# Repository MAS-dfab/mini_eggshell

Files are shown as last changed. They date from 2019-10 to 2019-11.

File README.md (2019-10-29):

# mini_Eggshell

Repository for the MAS1920 T1 Miniproject: mini_Eggshell

## Groups:
1. Laszlo, Edurne, Eliott
2. Yuhung, Maria, Remy
3. Ping, Jomana, Indra
4. Anton, Fatemeh, Emmanuelle
5. Chanon, Ioulios, Fred
6. Mahiro, Dinorah

## Schedule

[Find the latest schedule on Google Spreadsheets](https://docs.google.com/spreadsheets/d/181aZo1s0SwAvfoG4fKHYC5BHTWoBZZNCnyvJNnxfnJw/edit?usp=sharing)

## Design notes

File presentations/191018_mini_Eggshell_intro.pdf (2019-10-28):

# mini_Eggshell

## MAS T1 | 28.10.2019

## Introduction

## Eggshell

## Previous Miniprojects

## Assignment

## Schedule

## Ur online control

# Content

Gramazio Kohler Research
ETH Zurich

# Introduction

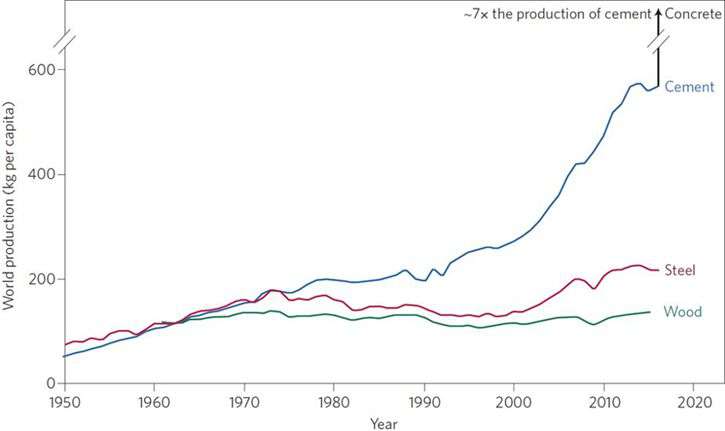
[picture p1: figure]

Gramazio Kohler Research

Paulo, Monteiro, Sabbie, Miller and Horvath (2017)

# Cost of a standard concrete element

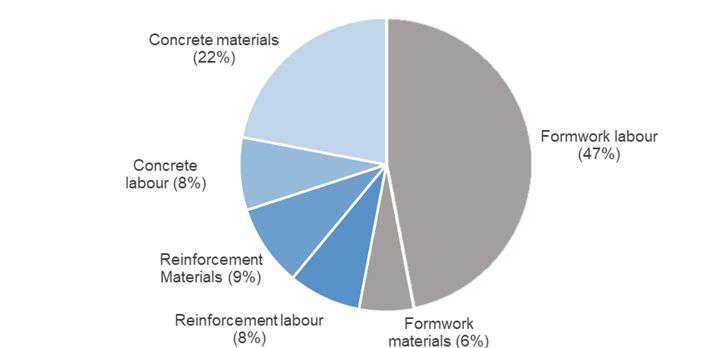
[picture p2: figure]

Gramazio Kohler Research

Lab (2007)

# Cost of a non-standard concrete element

Gramazio Kohler Research

Schipper and Grünewald (2014)

## xxx

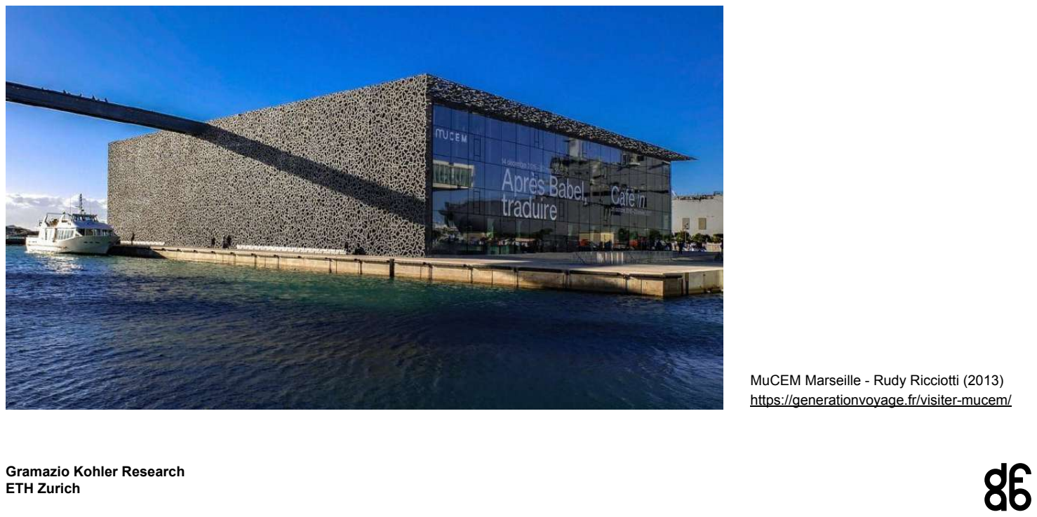
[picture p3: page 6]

Gramazio Kohler Research

MuCEM Marseille - Rudy Ricciotti (2013) https://generationvoyage.fr/visiter-mucem/

Gramazio Kohler Research

best of DETAIL 8 Beton/Concrete, Christian Schittich (2016)

# Eggshell concept

Gramazio Kohler Research

Ulrich (2017)

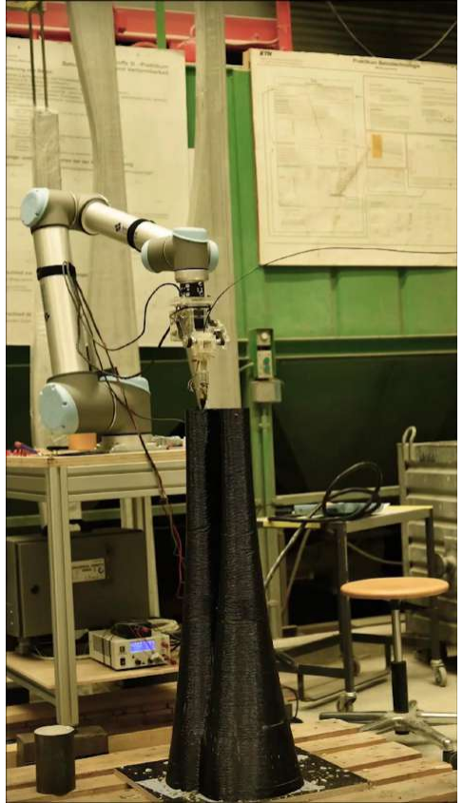
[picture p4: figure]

Gramazio Kohler Research

Gramazio Kohler Research (https://docs.google.com/file/d/1PcqgR71OjFk5ioSvPbPdr6lzZ_gwDWqv/preview)

# Simultaneous printing & filling

Gramazio Kohler Research

# Consecutive fabrication

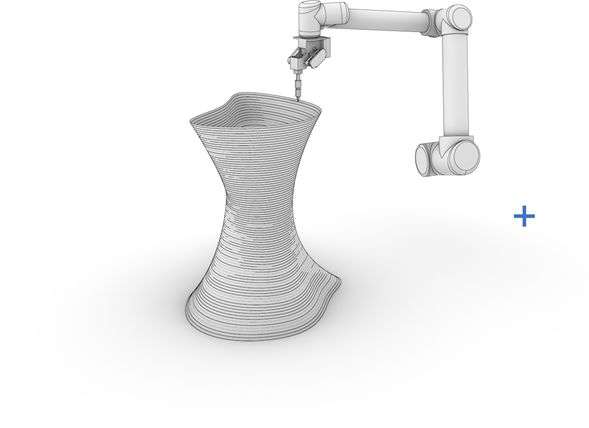
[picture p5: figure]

Gramazio Kohler Research

# Consecutive fabrication

Gramazio Kohler Research

# Consecutive fabrication

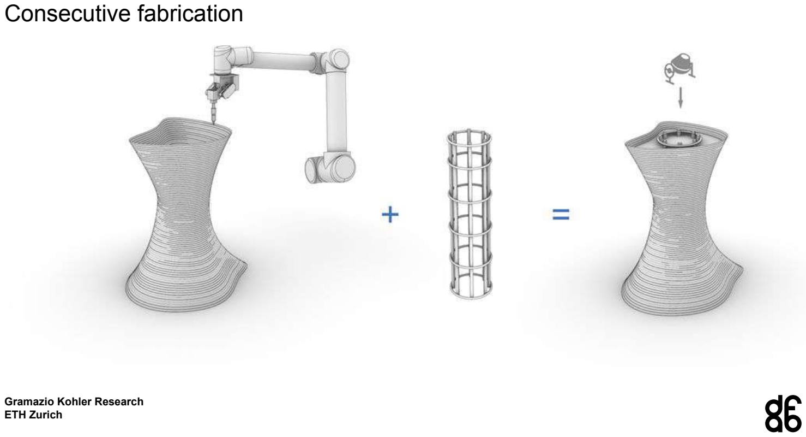
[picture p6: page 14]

Gramazio Kohler Research

# Basler & Hofmann

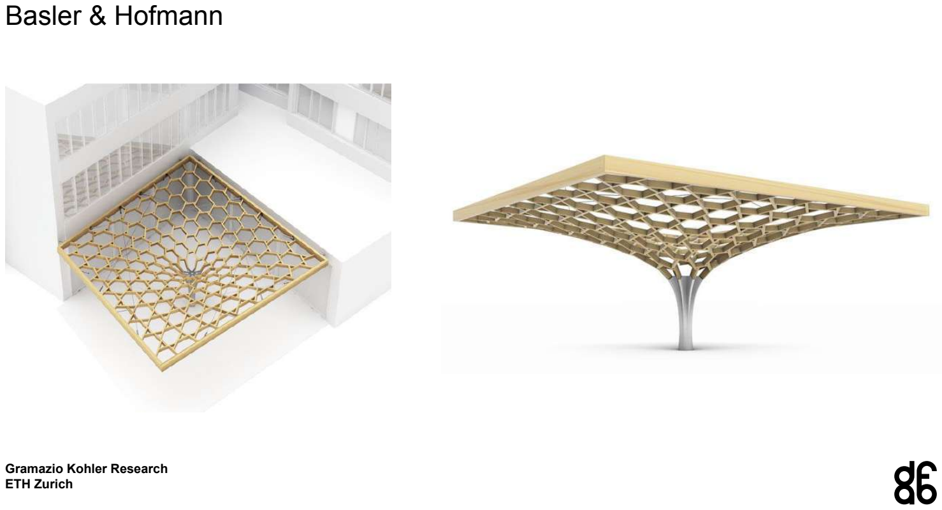
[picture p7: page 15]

Gramazio Kohler Research

Gramazio Kohler Research

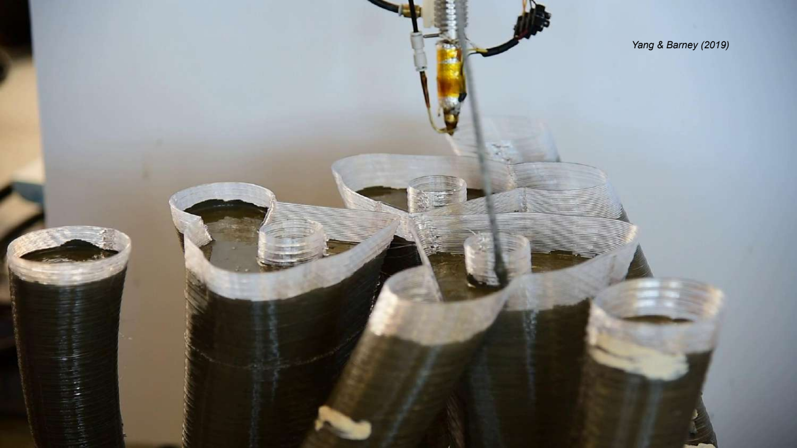
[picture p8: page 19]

Yang & Barney (2019) (https://docs.google.com/file/d/1zKKD6e-WPvSI6ZfkJOCtpLaU1aZg0VbD/preview)

minijammed is a three-week design and build assignment based on the ongoing research project Jammed Architectural Structures. The research focuses on the development of design and fabrication techniques to build fully reversible architectural structures by interlacing crushed-rock stones with textile string without any permanent bonding. The potential of the concept has been proven at architectural scale through the realisation of larger prototypes: Rock Print and Rock Print: A Manistone. minijammed invites the students to explore the design possibilities and the rich solution space of the method in a smaller scale.

The short-term project suggests a material-driven design and a robotic fabrication strategy, as only through the execution of multiple physical experiments, both manual and robotic, the designer is able to take informed decisions about the final outcome of the process.

# minijammed

Gramazio Kohler Research

Gramazio Kohler Research

minijammed: final exhibition

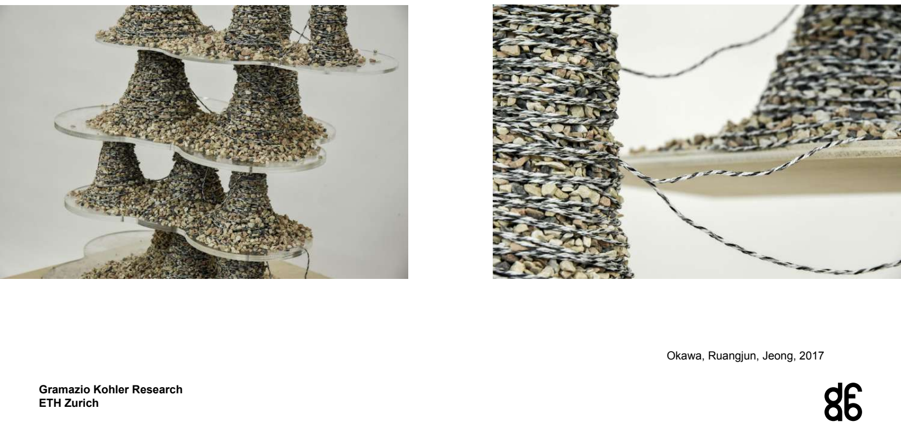
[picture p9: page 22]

Gramazio Kohler Research

Okawa, Ruangjun, Jeong, 2017

Gramazio Kohler Research

Pastrana, Su, Lin, Yoo, 2017

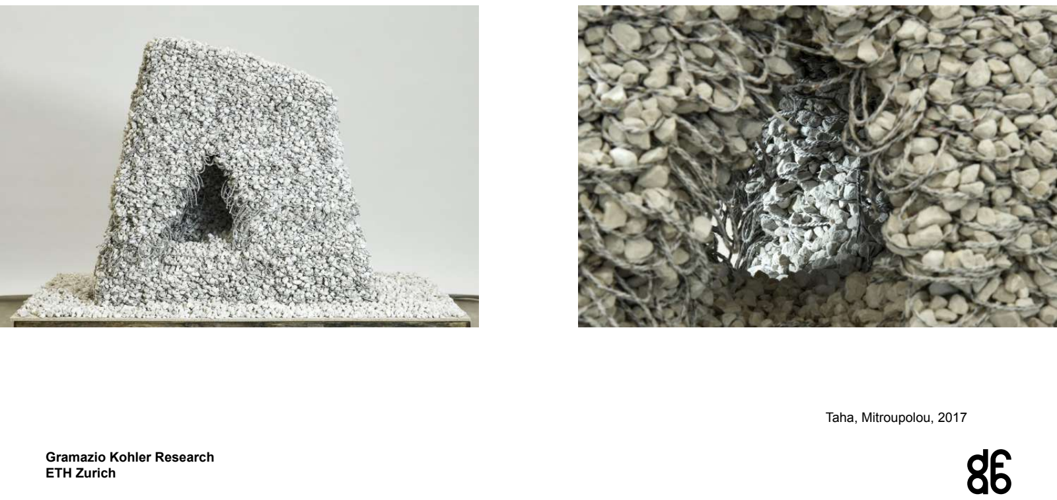
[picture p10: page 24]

Gramazio Kohler Research

Taha, Mitroupolou, 2017

Gramazio Kohler Research

Cena, Chousou, Wang, Wu, 2017

Rapid Clay Formations is a four-week design and build assignment investigating a novel fabrication process for malleable materials. Starting with the Remote Material Deposition installation in 2014, the Chair of Architecture and Digital Fabrication has investigated the idea of robotically positioning material in space from a distance and thereby creating differentiated architectural aggregations that are a direct expression of a dynamic and adaptive fabrication process. Continuing this concept, more recent projects developed within the MAS programme shifted the focus to the study of robotic fabrication processes for malleable materials, where the precise control of forces and positions applied to the material to design and build highly differentiated structures.

# Rapid Clay Formations

Gramazio Kohler Research

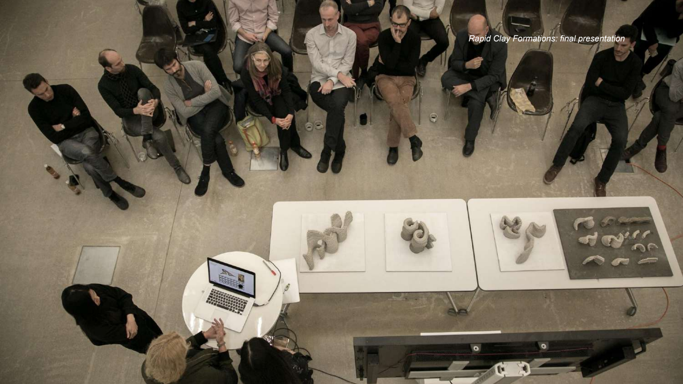
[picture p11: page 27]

Gramazio Kohler Research

Rapid Clay Formations: final presentation

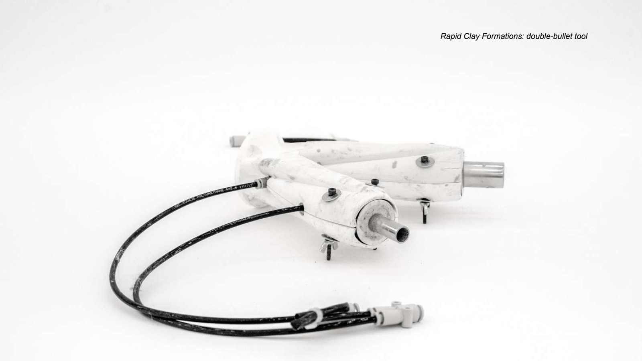
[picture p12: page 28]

Gramazio Kohler Research

Rapid Clay Formations: double-bullet tool

Gramazio Kohler Research

Akizuki, Barney, Du, 2018

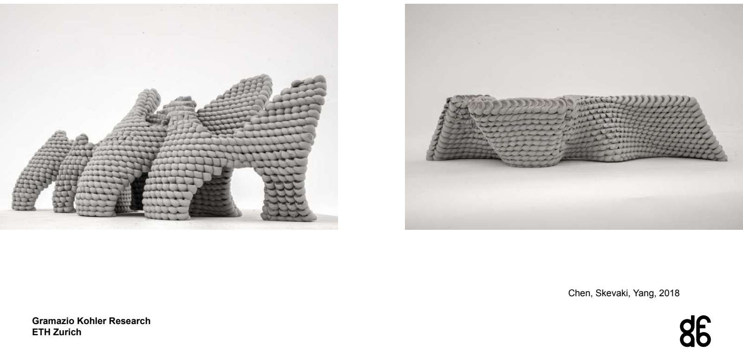
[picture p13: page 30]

Gramazio Kohler Research

Chen, Skevaki, Yang, 2018

Gramazio Kohler Research

v.d.Bulcke, Girish, Eftekhar, 2018

Use the Eggshell simultaneous printing & filling process to produce various building components.

## Two formwork material options

- | Clay | - 3 setups
- | Thermoplastic | - 3 setups

## Different building elements

## - Beam - Slab - Wall - Interface element (column - beam or wall - slab) - Column

# mini-eggshell: Assignment

Gramazio Kohler Research

## Focus on:

- | Structure | (reduce material/ weight, precise guides for reinforcement)
- | Function | (integrate different functions, lighting , media, electrical or mechanical services)
- | Performance | (integrate natural lighting and ventilation through transparency, porosity. Acoustics )
- | Aesthetics | (surface textures and ornamentation, architectural design, details)

# mini-eggshell: Goals

Gramazio Kohler Research

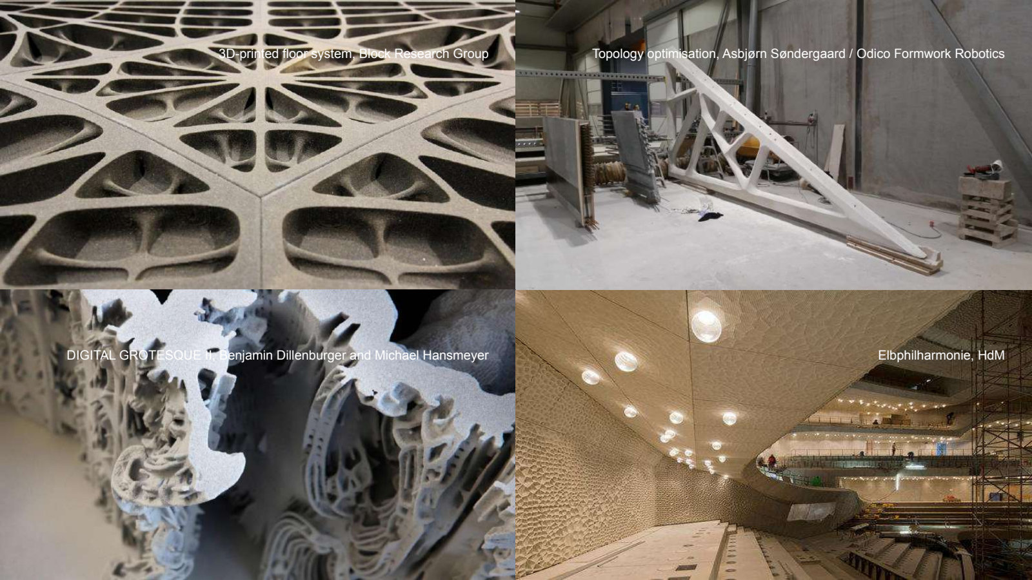
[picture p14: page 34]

3D-printed floor system, Block Research Group | Topology optimisation, Asbjørn Søndergaard / | Odico Formwork Robotics (https://www.odico.dk/?utm_medium=website&utm_source=archdaily.com)
DIGITAL GROTESQUE II, Benjamin Dillenburger and Michael Hansmeyer | Elbphilharmonie, HdM

# Schedule

Gramazio Kohler Research

https://docs.google.com/spreadsheets/d/181aZo1s0SwAvfoG4fKHYC5BHTWoBZZNCnyvJNnxfnJw/edit?usp=sharing

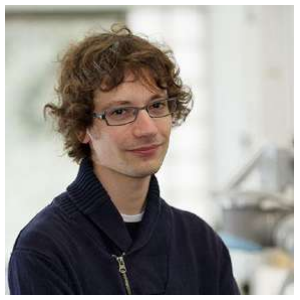
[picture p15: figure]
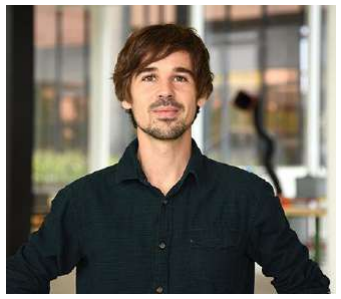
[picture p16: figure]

Dr. Lex Reiter (post-doc in PCBM) | Lukas Gebhard (PhD student with IBK) | Dr. Thibault Demoulin (post-doc at PCBM and Oxara)

# Guest Lectures

Gramazio Kohler Research

## - Grasshopper

# UR Online Control

### - JSON (https://en.wikipedia.org/wiki/JSON)

## - Python main file

Gramazio Kohler Research

# UR Online Control

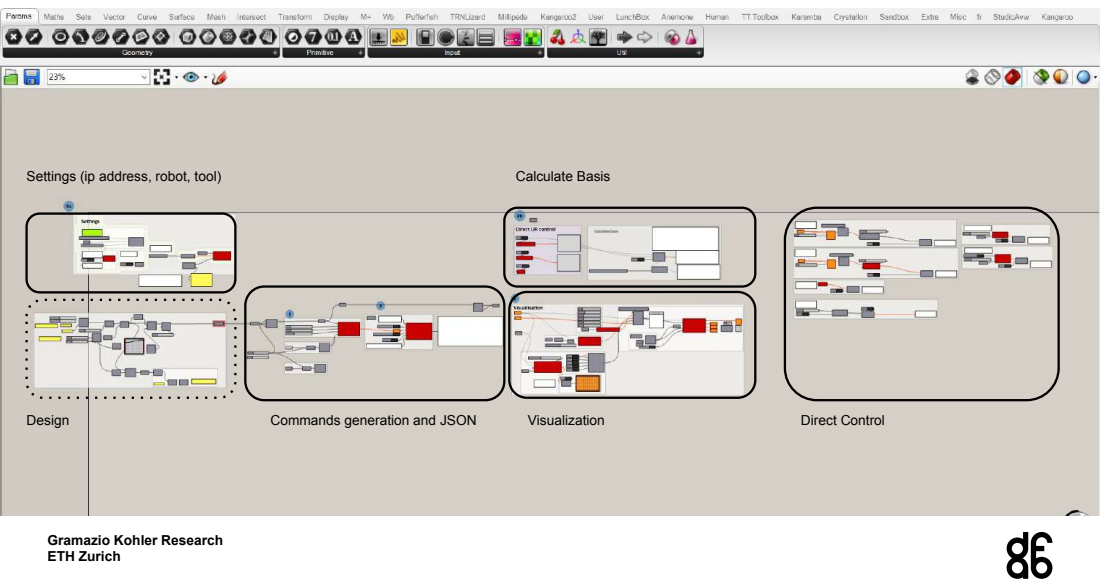
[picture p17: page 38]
Design; Commands generation and JSON; Visualization; Direct Control; Calculate Basis

Settings (ip address, robot, tool)

Gramazio Kohler Research

# UR Online Control

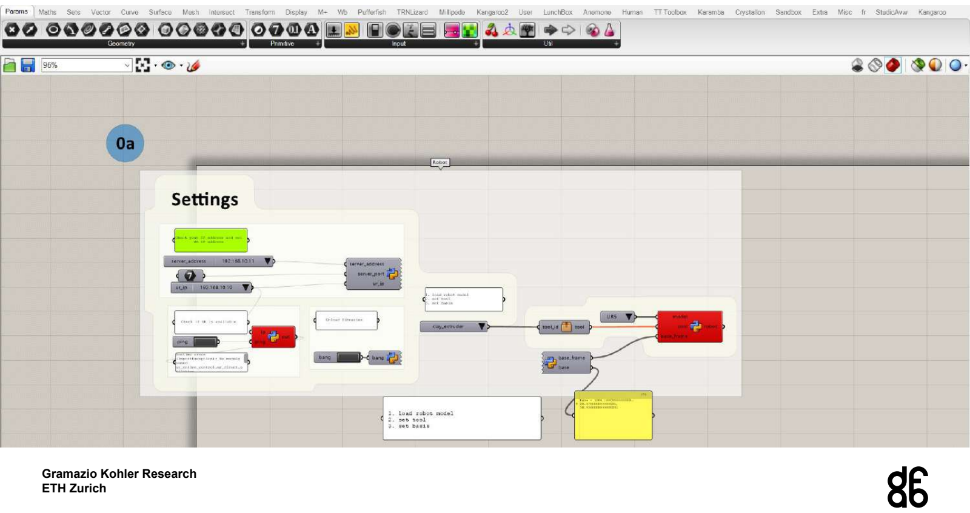
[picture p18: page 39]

Gramazio Kohler Research

# UR Online Control

Gramazio Kohler Research

# UR Online Control

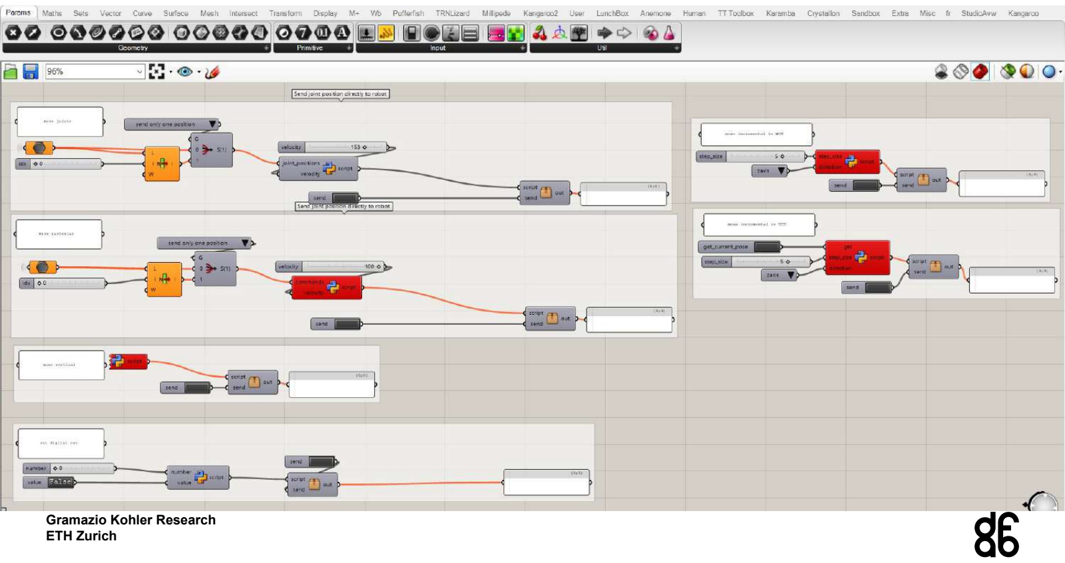
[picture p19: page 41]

Gramazio Kohler Research

# UR Online Control

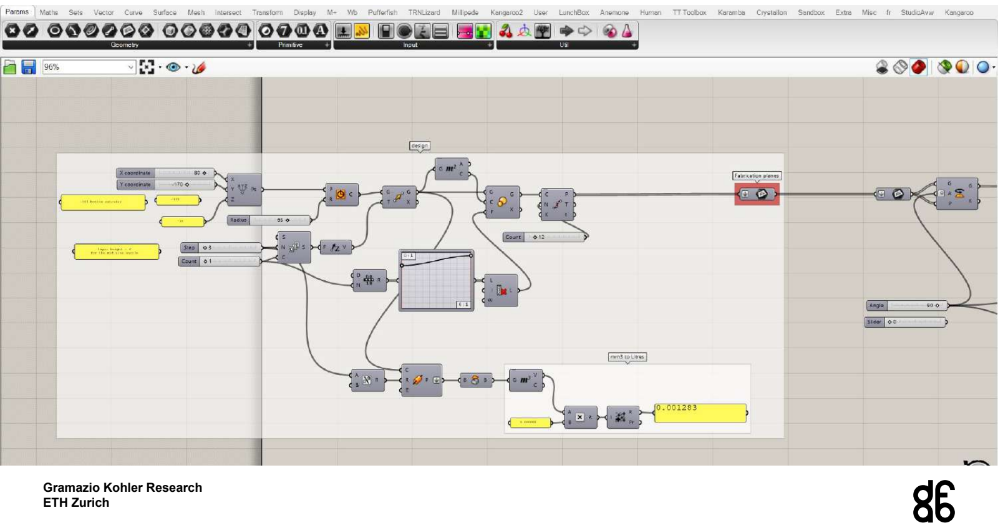
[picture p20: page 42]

Gramazio Kohler Research

# UR Online Control

Gramazio Kohler Research

# UR Online Control

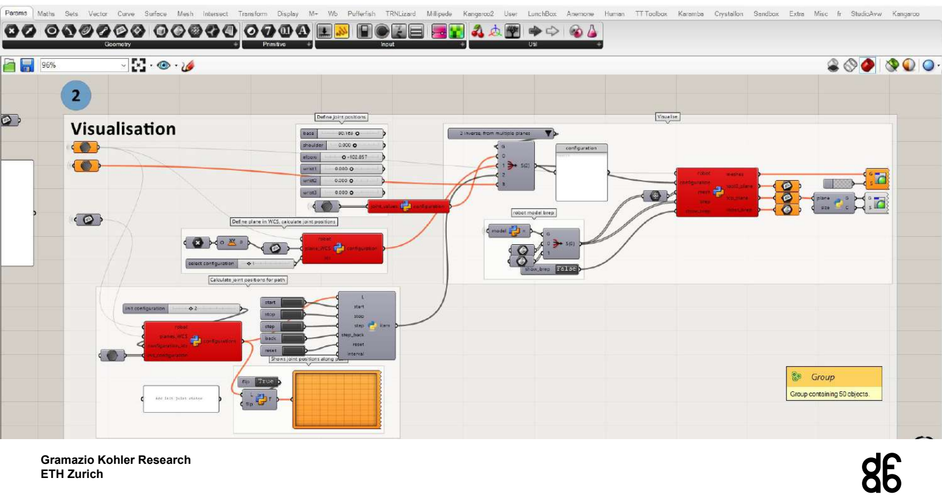
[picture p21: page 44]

Gramazio Kohler Research

# UR Online Control

Gramazio Kohler Research

# UR Online Control

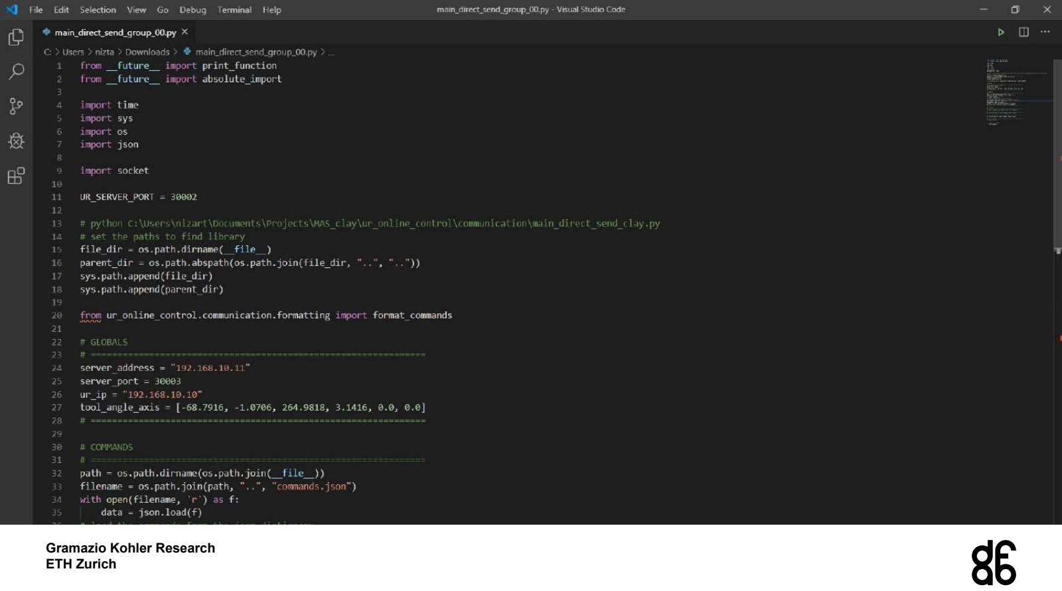
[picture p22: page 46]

Gramazio Kohler Research

# UR Online Control

Gramazio Kohler Research

# UR Online Control

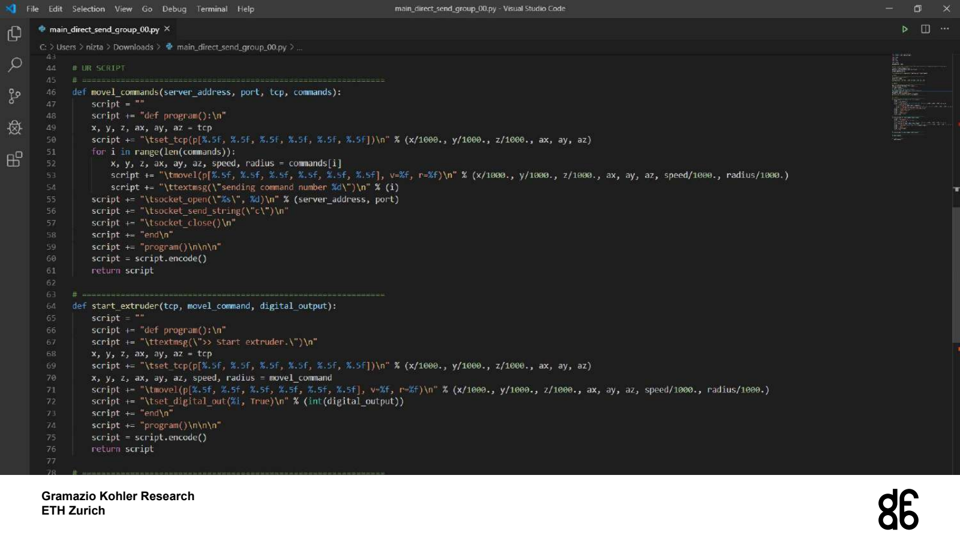
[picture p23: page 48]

Gramazio Kohler Research

# UR Online Control

Gramazio Kohler Research

# UR Online Control

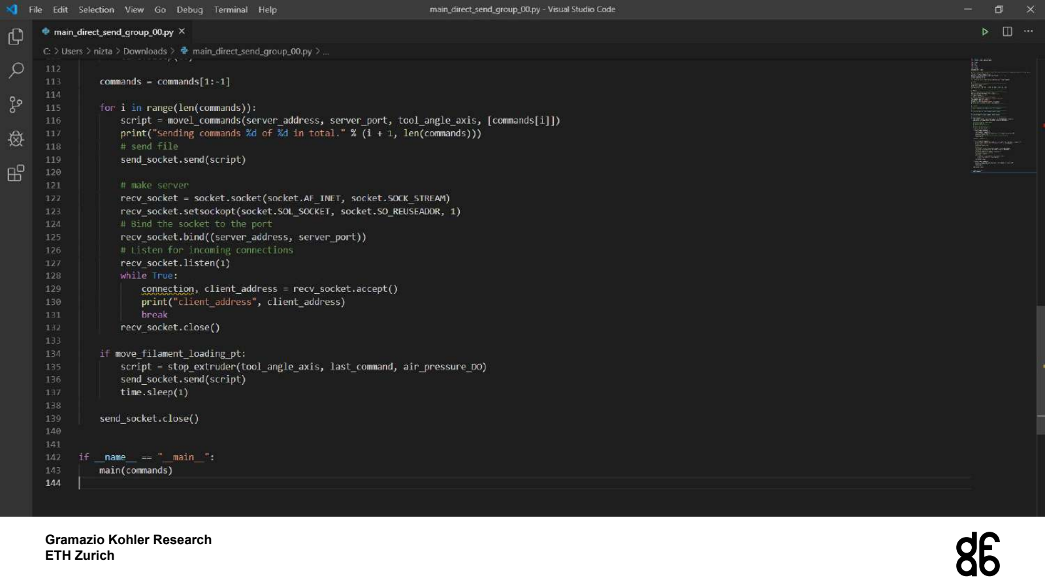
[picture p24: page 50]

Gramazio Kohler Research

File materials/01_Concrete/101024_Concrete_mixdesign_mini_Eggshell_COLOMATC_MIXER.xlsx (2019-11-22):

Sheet: M6
Mixture:
 |  | Weight | Density | Water content | Volume parts | Water weight |  | 1L
Sand | 0-4mm | 740 | 2.63 | 0 | 281.37 | 0 |  | 636.63
Cement | Normo5R | 982 | 3.1 | 0 | 316.77 | 0 |  | 844.83
Fly ash | Hydrolent | 165 | 2.3 | 0 | 71.74 | 0 |  | 141.95
Silicafume | MS 971U | 93 | 2.2 | 0 | 42.27 | 0 |  | 80.01
PVA 6mm | 6/0.15 | 13 | 1.3 | 0 | 10.00 | 0 |  | 11.18
PVA 12mm | 12/0.2 | 13 | 1.3 | 0 | 10.00 | 0 |  | 11.18
Water | Tap | 371 | 1 | 100 | 371.00 | 371 |  | 319.18
Superplasticizer | Glenium ACE30 | 4 | 1.06 | 70 | 3.77 | 2.8 |  | 3.44
Retarder | Succrose 30% | 2.7 | 1.05 | 70 | 2.57 | 1.89 |  | 2.32
Accelerator | X-Seed 100 | 60 | 1.135 | 78.5 | 52.86 | 47.1 |  | 51.62
 | SUM | 2443.7 | 2.102354706 |  | SUM | 422.79
 | V | 1162.363322
 | Exact calculation
 | Composition |  |  |  |  |  | Cement paste |  |  |  | Calculated properties: |  |  |  | Component properties: |  |  |  |  |  |  |  | 1 volume is mass of | On the volume given |  | mass
V | 30000 | mL |  |  |  |  | V [mL] | 14400 |  |  | Density [kg/m3] | 1912.0 |  |  |  | Density: | Solid content |  | Weight pure parts | Weight solution | Weight water | Volume solution | Solution | Solution | Solid | Water
Sand | 52 | % | Volume parts, all |  |  |  | w/b [-] | 0.4 | b |  | w/c [-] | 0.400 |  |  | CEM | 3.1 | 1 |  | 1 | 1 | 0 | 0.3225806452 | 1.234029847 | 17770.03 | 17770.03 | 0.00
PVA 6mm | 0 | % | Volume parts, all |  |  |  | FA[%] | 0 | b |  | Total weight [g]: | 27533.12 |  |  | FA | 2.3 | 1 |  | 0 | 0 | 0 | 0 | 0 | 0.00 | 0.00 | 0.00
PVA 12mm | 0 | % | Volume parts, all |  |  |  | MS[%] | 8 | b |  | Binder [g]: | 19315.25 |  |  | MS | 2.2 | 1 |  | 0.08695652174 | 0.08695652174 | 0 | 0.0395256917 | 0.1073069433 | 1545.22 | 1545.22 | 0.00
CEM | 92 | % | Weight binder |  |  |  | SP Glenium | 0.87 | b |  | All water [g] | 7726.10 |  |  | H20 | 1 | 0 | total | 0.4347826087 | 0.4057173913 | 0.4057173913 | 0.4057173913 | 0.5006673705 | 7209.61 | 0.00 | 7209.61
FA | 0 | % | Weight binder |  |  |  | RT | 0.35 | b |  |  |  |  |  | GleniumACE | 1.06 | 0.3 |  | 0.002836956522 | 0.009456521739 | 0.006619565217 | 0.008921246924 | 0.01166963008 | 168.04 | 50.41 | 117.63
MS | 8 | % | Weight binder |  |  |  | X-Seed | 0 | b |  |  |  |  |  | RT | 1.05 | 0.3 |  | 0.001141304348 | 0.003804347826 | 0.002663043478 | 0.003623188406 | 0.004694678768 | 67.60 | 20.28 | 47.32
Water | 0.4 | - | wb |  |  |  | C-100 | 4 | b |  |  |  |  |  | AC | 1.135 | 0.215 |  | 0 | 0 | 0 | 0 | 0 | 0.00 | 0.00 | 0.00
SP | 0.87 | % | weight_solution_adm/weight_dry_binder |  |  |  | Recipe: | weight [g]: |  | Content [kg/m3cementpaste] |  |  |  |  | C-100 | 1.45 | 0.545 |  | 0.02369565217 | 0.04347826087 | 0.0197826087 | 0.0299850075 | 0.05365347163 | 772.61 | 421.07 | 351.54
RT | 0.35 | % | weight_solution_adm/weight_dry_binder |  |  |  | CEM | 17770.03 |  | 1234.03 | as solution
X-Seed 100 | 0 | % | weight_solution_adm/weight_dry_binder |  |  |  | FA | 0.00 |  | 0.00 |  |  |  |  |  |  |  | SUM | 1.549413043 |  | 0.4347826087 | 0.810353171 |  |  |  | 7726.10
C-100 | 4 | % | weight_solution_adm/weight_dry_binder |  |  |  | MS | 1545.22 |  | 107.31
 | Components |  |  |  |  |  | H2O | 7209.61 |  | 500.67 |  |  |  |  |  |  |  |  | Weight binder
Sand | 0-4mm | 2.63 | 0 |  |  |  | ACE30 | 168.04 |  | 11.67 |  |  |  |  |  |  |  |  | 1.086956522
CEM | Normo5R | 3.1 | 0 |  |  |  | RT | 67.60 |  | 4.69
FA | Hydrolent | 2.3 | 0 |  |  |  | AC | 0.00 |  | 0.00
MS | MS 971U | 2.2 | 0 |  |  |  | C-100 | 772.61 |  | 53.65 |  |  |  |  | Mortar component volumes
H2O | Tap | 1 | 100 |  |  |  | Mortar |  |  |  |  |  |  |  | Volume | Weight | Density
ACE30 | Glenium ACE30 | 1.06 | 70 |  |  |  | V [mL] | 30000 |  |  |  |  |  |  | 14400 | 27533.12 | 1.91
RT | Succrose 30% | 1.05 | 70 |  |  |  | C_Sand | 52 | % |  |  |  |  |  | 15600 | 41028 | 2.63
AC | X-Seed 100 | 1.135 | 78.5 |  |  |  | C_PVA6mm | 0 | % |  |  |  |  |  | 0 | 0 | 1.30
C-100 | C-100 | 1.45 | 45.5 |  |  |  | C_PVA12mm | 0 | % |  |  |  |  |  | 0 | 0 | 1.30
PVA6mm | 6/0.15 | 1.3 | 0 |  |  |  |  |  |  | solution | pure
PVA12mm | 12/0.2 | 1.3 | 0 |  |  |  | Recipe | g | (6L) | Content [kg/m3mortar] | Content | Volume | Before acceleration
 |  |  |  |  |  |  | Sand | 41028.00 |  | 1367.60 | 1367.60 | 520.00 | wb | 0.377
 |  |  |  |  |  |  | CEM | 17770.03 |  | 592.33 | 592.33 | 191.08
 | 0.0649 |  |  |  |  |  | FA | 0.00 |  | 0.00 | 0.00 | 0.00
 | 1.0403 | 0.3467666667 |  |  |  |  | MS | 1545.22 |  | 51.51 | 51.51 | 23.41
 | 2.027 | 1.351333333 |  |  |  |  | H2O | 7209.61 |  | 240.32 | 257.54 | 240.32
 |  |  |  |  |  |  | ACE30 | 168.04 |  | 5.60 | 1.68 | 5.28
 |  |  |  |  |  |  | Sucrose | 67.60 |  | 2.25 | 0.68 | 2.15
 |  |  |  |  |  |  | X-Seed | 0.00 |  | 0.00 | 0.00 | 0.00
 |  |  |  |  |  |  | C-100 | 772.61 |  | 25.75 | 14.04 | 17.76
Used compositions:
Standard Mixture:
V | 1000
Sand | 24.21
PVA 6mm | 0.8603
PVA 12mm | 0.8603
CEM | 79.19
FA | 13.31 |  |  |  |  |  |  |  | Density | 2285.37 | kg/m3
MS | 7.5
Water | 0.341
SP | 0.0968
RT | 0.0653
AC | 1.0403
Print this:
 | Composition
V | 30000 | mL
Sand | 52 | % | Volume parts, all
PVA 6mm | 0 | % | Volume parts, all
PVA 12mm | 0 | % | Volume parts, all
CEM | 92 | % | Weight binder
FA | 0 | % | Weight binder
MS | 8 | % | Weight binder
Water | 0.4 | - | wb
SP | 0.87 | % | weight_solution_adm/weight_dry_binder
RT | 0.35 | % | weight_solution_adm/weight_dry_binder
X-Seed 100 | 0 | % | weight_solution_adm/weight_dry_binder
C-100 | 4 | % | weight_solution_adm/weight_dry_binder
Recipe | Mass [g] | 30 | L
Sand | 41028.0
CEM | 17770.0
FA | 0.0
MS | 1545.2
H2O | 7209.6
ACE30 | 168.04
Sucrose | 67.60
X-Seed | 0.00
C-100 | 772.61

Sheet: Print
 |  | Composition
Volume |  | 30000 | mL | <--- edit this field |  | MIXDESIGN FOR COLOMATIC MIXER (LESS SP)
AGGREGATES
Sand | 0-4mm | 52 | %
Cement | Normo 5R | 92 | % |  |  | ACCELERATION TABLE
Microsilica | Masterlife | 8 | % |  |  | For these liters of final product | 0.10 | L | For these liters of final product | 1.00 | L
 |  |  |  |  |  | Mass of retarded | 0.229 | kg | Mass of retarded | 2.285 | kg
ADMIXTURES |  |  |  |  |  | Mass of accelerator C-100 | 2.45 | g | Mass of accelerator C-100 | 24.53 | g
Water |  | 0.4 | -
Superplasticizer | BASF MasterGlenium ACE30 | 0.87 | % |  |  | For these liters of final product | 0.25 | L | For these liters of final product | 2.00 | L
Sucrose | 70% water / 30% sugar | 0.35 | % |  |  | Mass of retarded | 0.571 | kg | Mass of retarded | 4.571 | kg
 |  |  |  |  |  | Mass of accelerator C-100 | 6.13 | g | Mass of accelerator C-100 | 49.06 | g
ACCELERATOR
Accelerator | SIKA C-100 | 4 | % |  |  | For these liters of final product | 0.50 | L | For these liters of final product | 3.00 | L
 |  |  |  |  |  | Mass of retarded | 1.143 | kg | Mass of retarded | 6.856 | kg
Recipe |  | Mass [g] |  |  |  | Mass of accelerator C-100 | 12.27 | g | Mass of accelerator C-100 | 73.59 | g
AGGREGATES
Sand | 0-4mm | 41028.0 | g
Cement | Normo 5R | 17770.0 | g
Microsilica | Masterlife | 1545.2 | g
ADMIXTURES
Water |  | 7209.6 | g
Superplasticizer | BASF MasterGlenium ACE30 | 168.04 | g
Sucrose | 70% water / 30% sugar | 67.60 | g
ACCELERATOR
Accelerator | SIKA C-100 | 772.61 | g
Sum of mass |  | 68561.1 | Density | 2.29 | g/cm3
Accelerator amount |  |  | 24.53 | g/L
Mass before acceleration |  |  | 67788.5 | g
Mass of accelerator |  |  | 772.61 | g

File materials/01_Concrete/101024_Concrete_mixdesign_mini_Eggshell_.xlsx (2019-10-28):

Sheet: M6
Mixture:
 |  | Weight | Density | Water content | Volume parts | Water weight |  | 1L
Sand | 0-4mm | 740 | 2.63 | 0 | 281.37 | 0 |  | 636.63
Cement | Normo5R | 982 | 3.1 | 0 | 316.77 | 0 |  | 844.83
Fly ash | Hydrolent | 165 | 2.3 | 0 | 71.74 | 0 |  | 141.95
Silicafume | MS 971U | 93 | 2.2 | 0 | 42.27 | 0 |  | 80.01
PVA 6mm | 6/0.15 | 13 | 1.3 | 0 | 10.00 | 0 |  | 11.18
PVA 12mm | 12/0.2 | 13 | 1.3 | 0 | 10.00 | 0 |  | 11.18
Water | Tap | 371 | 1 | 100 | 371.00 | 371 |  | 319.18
Superplasticizer | Glenium ACE30 | 4 | 1.06 | 70 | 3.77 | 2.8 |  | 3.44
Retarder | Succrose 30% | 2.7 | 1.05 | 70 | 2.57 | 1.89 |  | 2.32
Accelerator | X-Seed 100 | 60 | 1.135 | 78.5 | 52.86 | 47.1 |  | 51.62
 | SUM | 2443.7 | 2.102354706 |  | SUM | 422.79
 | V | 1162.363322
 | Exact calculation
 | Composition |  |  |  |  |  | Cement paste |  |  |  | Calculated properties: |  |  |  | Component properties: |  |  |  |  |  |  |  | 1 volume is mass of | On the volume given |  | mass
V | 10000 | mL |  |  |  |  | V [mL] | 4800 |  |  | Density [kg/m3] | 1912.0 |  |  |  | Density: | Solid content |  | Weight pure parts | Weight solution | Weight water | Volume solution | Solution | Solution | Solid | Water
Sand | 52 | % | Volume parts, all |  |  |  | w/b [-] | 0.4 | b |  | w/c [-] | 0.400 |  |  | CEM | 3.1 | 1 |  | 1 | 1 | 0 | 0.3225806452 | 1.233969418 | 5923.05 | 5923.05 | 0.00
PVA 6mm | 0 | % | Volume parts, all |  |  |  | FA[%] | 0 | b |  | Total weight [g]: | 9177.55 |  |  | FA | 2.3 | 1 |  | 0 | 0 | 0 | 0 | 0 | 0.00 | 0.00 | 0.00
PVA 12mm | 0 | % | Volume parts, all |  |  |  | MS[%] | 8 | b |  | Binder [g]: | 6438.10 |  |  | MS | 2.2 | 1 |  | 0.08695652174 | 0.08695652174 | 0 | 0.0395256917 | 0.1073016885 | 515.05 | 515.05 | 0.00
CEM | 92 | % | Weight binder |  |  |  | SP Glenium | 0.885 | b |  | All water [g] | 2575.24 |  |  | H20 | 1 | 0 | total | 0.4347826087 | 0.4056032609 | 0.4056032609 | 0.4056032609 | 0.5005020198 | 2402.41 | 0.00 | 2402.41
FA | 0 | % | Weight binder |  |  |  | RT | 0.35 | b |  |  |  |  |  | GleniumACE | 1.06 | 0.3 |  | 0.002885869565 | 0.009619565217 | 0.006733695652 | 0.009075061526 | 0.01187024929 | 56.98 | 17.09 | 39.88
MS | 8 | % | Weight binder |  |  |  | X-Seed | 0 | b |  |  |  |  |  | RT | 1.05 | 0.3 |  | 0.001141304348 | 0.003804347826 | 0.002663043478 | 0.003623188406 | 0.004694448874 | 22.53 | 6.76 | 15.77
Water | 0.4 | - | wb |  |  |  | C-100 | 4 | b |  |  |  |  |  | AC | 1.135 | 0.215 |  | 0 | 0 | 0 | 0 | 0 | 0.00 | 0.00 | 0.00
SP | 0.885 | % | weight_solution_adm/weight_dry_binder |  |  |  | Recipe: | weight [g]: |  | Content [kg/m3cementpaste] |  |  |  |  | C-100 | 1.45 | 0.545 |  | 0.02369565217 | 0.04347826087 | 0.0197826087 | 0.0299850075 | 0.05365084427 | 257.52 | 140.35 | 117.17
RT | 0.35 | % | weight_solution_adm/weight_dry_binder |  |  |  | CEM | 5923.05 |  | 1233.97 | as solution
X-Seed 100 | 0 | % | weight_solution_adm/weight_dry_binder |  |  |  | FA | 0.00 |  | 0.00 |  |  |  |  |  |  |  | SUM | 1.549461957 |  | 0.4347826087 | 0.8103928552 |  |  |  | 2575.24
C-100 | 4 | % | weight_solution_adm/weight_dry_binder |  |  |  | MS | 515.05 |  | 107.30
 | Components |  |  |  |  |  | H2O | 2402.41 |  | 500.50 |  |  |  |  |  |  |  |  | Weight binder
Sand | 0-4mm | 2.63 | 0 |  |  |  | ACE30 | 56.98 |  | 11.87 |  |  |  |  |  |  |  |  | 1.086956522
CEM | Normo5R | 3.1 | 0 |  |  |  | RT | 22.53 |  | 4.69
FA | Hydrolent | 2.3 | 0 |  |  |  | AC | 0.00 |  | 0.00
MS | MS 971U | 2.2 | 0 |  |  |  | C-100 | 257.52 |  | 53.65 |  |  |  |  | Mortar component volumes
H2O | Tap | 1 | 100 |  |  |  | Mortar |  |  |  |  |  |  |  | Volume | Weight | Density
ACE30 | Glenium ACE30 | 1.06 | 70 |  |  |  | V [mL] | 10000 |  |  |  |  |  |  | 4800 | 9177.55 | 1.91
RT | Succrose 30% | 1.05 | 70 |  |  |  | C_Sand | 52 | % |  |  |  |  |  | 5200 | 13676 | 2.63
AC | X-Seed 100 | 1.135 | 78.5 |  |  |  | C_PVA6mm | 0 | % |  |  |  |  |  | 0 | 0 | 1.30
C-100 | C-100 | 1.45 | 45.5 |  |  |  | C_PVA12mm | 0 | % |  |  |  |  |  | 0 | 0 | 1.30
PVA6mm | 6/0.15 | 1.3 | 0 |  |  |  |  |  |  | solution | pure
PVA12mm | 12/0.2 | 1.3 | 0 |  |  |  | Recipe | g | (6L) | Content [kg/m3mortar] | Content | Volume | Before acceleration
 |  |  |  |  |  |  | Sand | 13676.00 |  | 1367.60 | 1367.60 | 520.00 | wb | 0.377
 |  |  |  |  |  |  | CEM | 5923.05 |  | 592.31 | 592.31 | 191.07
 | 0.0649 |  |  |  |  |  | FA | 0.00 |  | 0.00 | 0.00 | 0.00
 | 1.0403 | 0.3467666667 |  |  |  |  | MS | 515.05 |  | 51.50 | 51.50 | 23.41
 | 2.027 | 1.351333333 |  |  |  |  | H2O | 2402.41 |  | 240.24 | 257.52 | 240.24
 |  |  |  |  |  |  | ACE30 | 56.98 |  | 5.70 | 1.71 | 5.38
 |  |  |  |  |  |  | Sucrose | 22.53 |  | 2.25 | 0.68 | 2.15
 |  |  |  |  |  |  | X-Seed | 0.00 |  | 0.00 | 0.00 | 0.00
 |  |  |  |  |  |  | C-100 | 257.52 |  | 25.75 | 14.04 | 17.76
Used compositions:
Standard Mixture:
V | 1000
Sand | 24.21
PVA 6mm | 0.8603
PVA 12mm | 0.8603
CEM | 79.19
FA | 13.31 |  |  |  |  |  |  |  | Density | 2285.35 | kg/m3
MS | 7.5
Water | 0.341
SP | 0.0968
RT | 0.0653
AC | 1.0403
Print this:
 | Composition
V | 10000 | mL
Sand | 52 | % | Volume parts, all
PVA 6mm | 0 | % | Volume parts, all
PVA 12mm | 0 | % | Volume parts, all
CEM | 92 | % | Weight binder
FA | 0 | % | Weight binder
MS | 8 | % | Weight binder
Water | 0.4 | - | wb
SP | 0.885 | % | weight_solution_adm/weight_dry_binder
RT | 0.35 | % | weight_solution_adm/weight_dry_binder
X-Seed 100 | 0 | % | weight_solution_adm/weight_dry_binder
C-100 | 4 | % | weight_solution_adm/weight_dry_binder
Recipe | Mass [g] | 10 | L
Sand | 13676.0
CEM | 5923.1
FA | 0.0
MS | 515.0
H2O | 2402.4
ACE30 | 56.98
Sucrose | 22.53
X-Seed | 0.00
C-100 | 257.52

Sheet: Print
 |  | Composition
Volume |  | 10000 | mL | <--- edit this field
AGGREGATES
Sand | 0-4mm | 52 | %
Cement | Normo 5R | 92 | % |  |  | ACCELERATION TABLE
Microsilica | Masterlife | 8 | % |  |  | For these liters of final product | 0.10 | L | For these liters of final product | 1.00 | L
 |  |  |  |  |  | Mass of retarded | 0.229 | kg | Mass of retarded | 2.285 | kg
ADMIXTURES |  |  |  |  |  | Mass of accelerator C-100 | 2.45 | g | Mass of accelerator C-100 | 24.53 | g
Water |  | 0.4 | -
Superplasticizer | BASF MasterGlenium ACE30 | 0.885 | % |  |  | For these liters of final product | 0.25 | L | For these liters of final product | 2.00 | L
Sucrose | 70% water / 30% sugar | 0.35 | % |  |  | Mass of retarded | 0.571 | kg | Mass of retarded | 4.571 | kg
 |  |  |  |  |  | Mass of accelerator C-100 | 6.13 | g | Mass of accelerator C-100 | 49.06 | g
ACCELERATOR
Accelerator | SIKA C-100 | 4 | % |  |  | For these liters of final product | 0.50 | L | For these liters of final product | 3.00 | L
 |  |  |  |  |  | Mass of retarded | 1.143 | kg | Mass of retarded | 6.856 | kg
Recipe |  | Mass [g] |  |  |  | Mass of accelerator C-100 | 12.27 | g | Mass of accelerator C-100 | 73.59 | g
AGGREGATES
Sand | 0-4mm | 13676.0 | g
Cement | Normo 5R | 5923.1 | g
Microsilica | Masterlife | 515.0 | g
ADMIXTURES
Water |  | 2402.4 | g
Superplasticizer | BASF MasterGlenium ACE30 | 56.98 | g
Sucrose | 70% water / 30% sugar | 22.53 | g
ACCELERATOR
Accelerator | SIKA C-100 | 257.52 | g
Sum of mass |  | 22853.5 | Density | 2.29 | g/cm3
Accelerator amount |  |  | 24.53 | g/L
Mass before acceleration |  |  | 22596.0 | g
Mass of accelerator |  |  | 257.52 | g

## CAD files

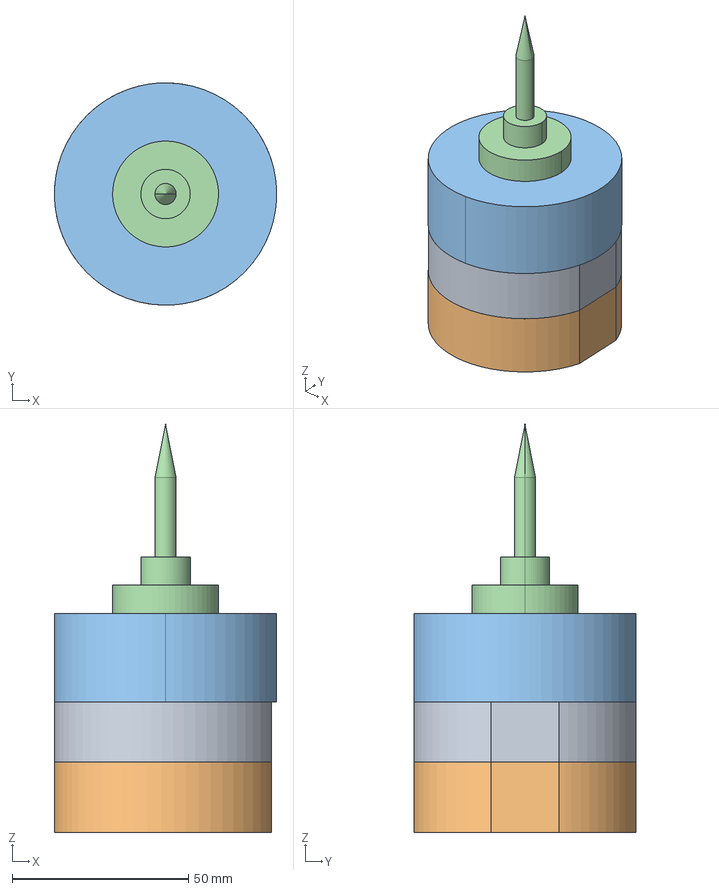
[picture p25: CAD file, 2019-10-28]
ur_online_control/ur/tools/models/measurement_tool.stp
63.0 x 63.0 x 115.6 mm

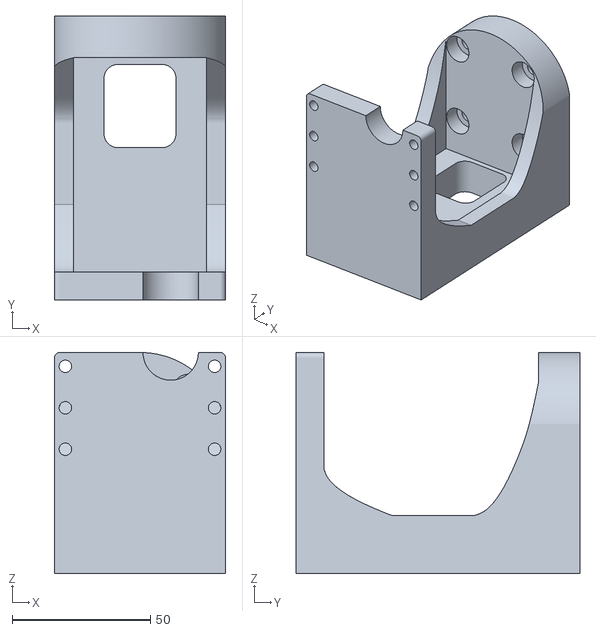
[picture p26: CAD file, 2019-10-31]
hardware/02_Plastic extruder/191030_plastic_extruder.stl
62.0 x 102.6 x 80.0

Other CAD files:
design/group_04/Base.3dm
design/group_05/191101_BaseTableConfiguration.3dm
design/group_05/191111_BaseTableConfiguration_geometriesBC.3dm
design/group_05/191115_BaseTableConfiguration_geometriesBC.3dm
hardware/01_Clay extruder/clay_extruder_endEffector_V5.3dm
hardware/03_Bachmann_ur_base/bachmann_ur_base.3dm
hardware/04_filament wooden stand and printing table/Pole Filament Prototype.3dm
ur_online_control/ur/tools/models/measurement_tool.obj

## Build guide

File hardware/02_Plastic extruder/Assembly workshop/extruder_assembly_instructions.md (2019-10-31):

Supervolcano

# Extruder assembly workshop

## What's in the box?

- E3D Titan Aero Extruder
- E3D SuperVolcano Hot End
- Nema 17 Stepper Motor
- Arduino UNO/MEGA
- TB6600 compatible Stepper Motor Driver
- 24V DC Power Supply
- 15A 400W MOSFET Driver 5-36V x2
- Bread board mini
- Relay 
- 100k Ohm resistor
- Jumper cables

## Required tools
- Hex screw driver
- Flathead screw driver
- Cross screw driver
- Drill
- (Potentiometer)

## Helpful tutorials
- Stepper motor with Arduino: https://www.makerguides.com/tb6600-stepper-motor-driver-arduino-tutorial/
- Build a heater with Arduino: https://www.alanzucconi.com/2016/08/02/arduino-heater-2/#introduction
- Basic arduino tutorials: https://www.arduino.cc/en/Tutorial/Foundations

## **IMPORTANT**
- Do not work with electronics when power is plugged in.
- Try to make good electrical connections, especially to the 24V power supply. Ask us for the crimping tool so we can make sure the connection is solid.

## Extruder assembly instructions

1. Assemble the Titan Aero Extruder according to the following instructions: https://e3d-online.dozuki.com/Guide/Titan+Aero+Assembly/23  
Start from *Step 14: Gather Titan Body* as we will be assembling the SuperVolcano nozzle in a second step.

    Notes:
    - In Step 15 do not use the M3 set screw that is supplied within the package, instead use one that we provide (ask us.)
    - In Step 32 it can be difficult to put in the screw with the washer. If it does not work, first try to slightly flatten the washer and try again. If it still does not work, leave the washer out but do not tighten the screw too tight as this can damage the bearings. 

1. Assemble the SuperVolcano heating block according to the following instructions: https://e3d-online.dozuki.com/Guide/Super+Volcano+Assembly/82

1. Connect cables to the fan and thermistor (using the sugarcubes), connect the supplied stepper motor cable and the heating cable using the Plug connection. Ask us for the rest of the required cables.

## Electronics box preparations

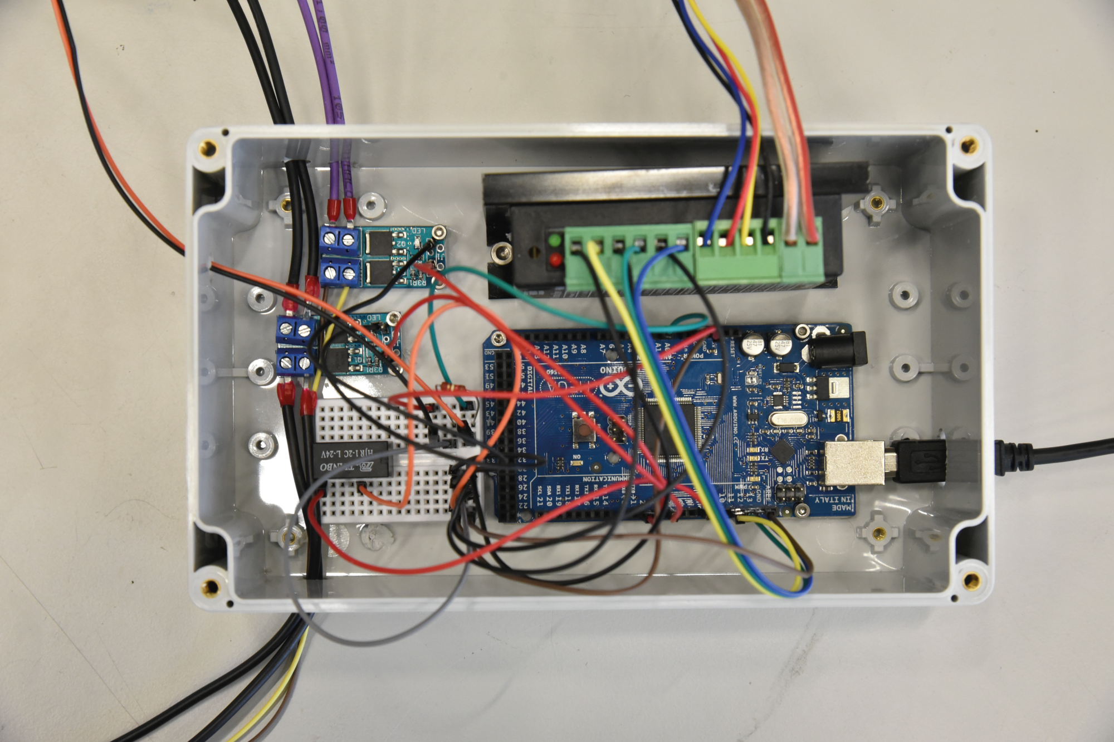
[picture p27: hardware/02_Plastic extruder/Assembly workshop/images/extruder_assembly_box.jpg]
assembly box


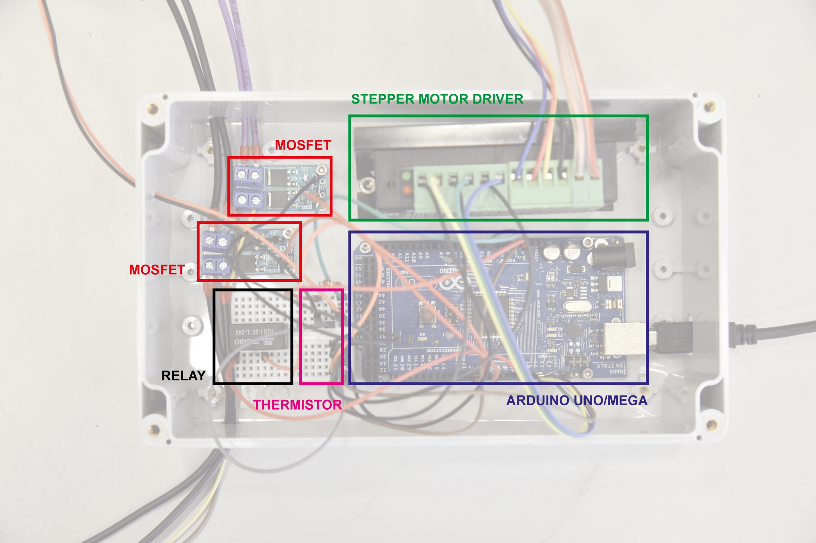
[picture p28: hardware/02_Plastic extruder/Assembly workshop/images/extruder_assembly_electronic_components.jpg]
electronics


1. Place the components in the box according to the following picture. First place the electronics without fastening them to see what is the correct fit. After fitting all of the components, mark the holes on the bottom of the box with a pen and drill the holes with a 3mm drill. After drilling the holes you can put in the various components. Use M2.5 bolts and nuts for the electrical components and M4 bolts for the stepper driver.

1. Drill holes in the outside of the box for inputing cables. See the example for one possible way of doing it. 

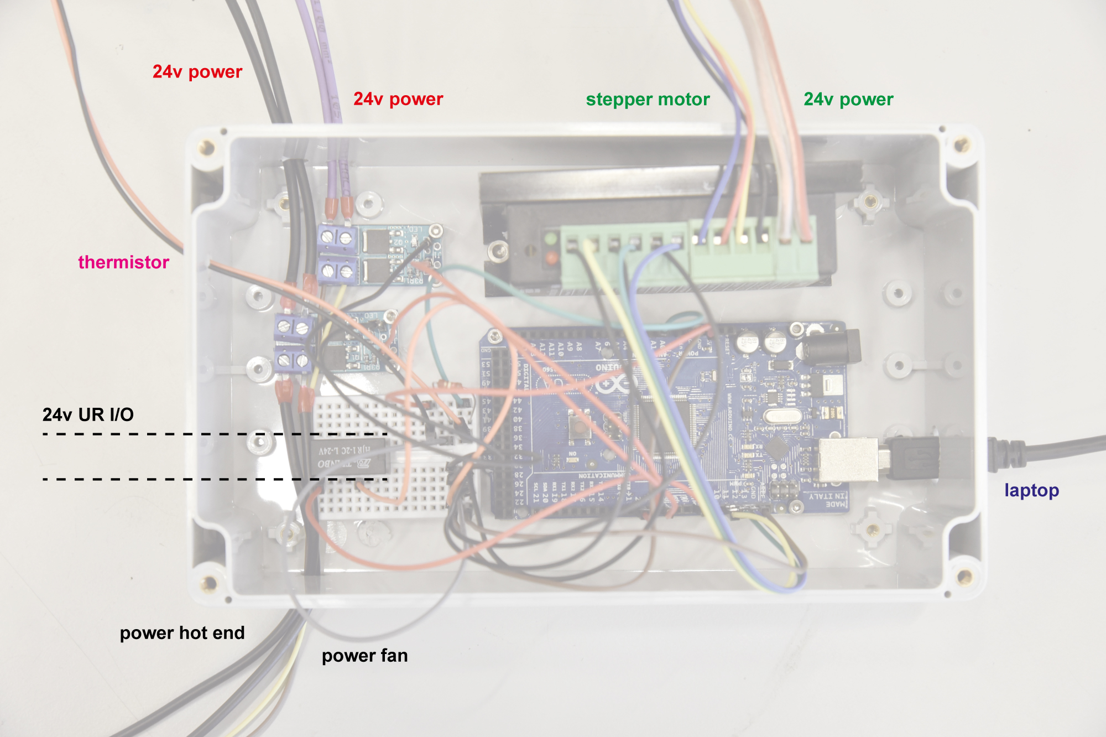
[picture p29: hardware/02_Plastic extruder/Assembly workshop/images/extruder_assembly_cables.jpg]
cables


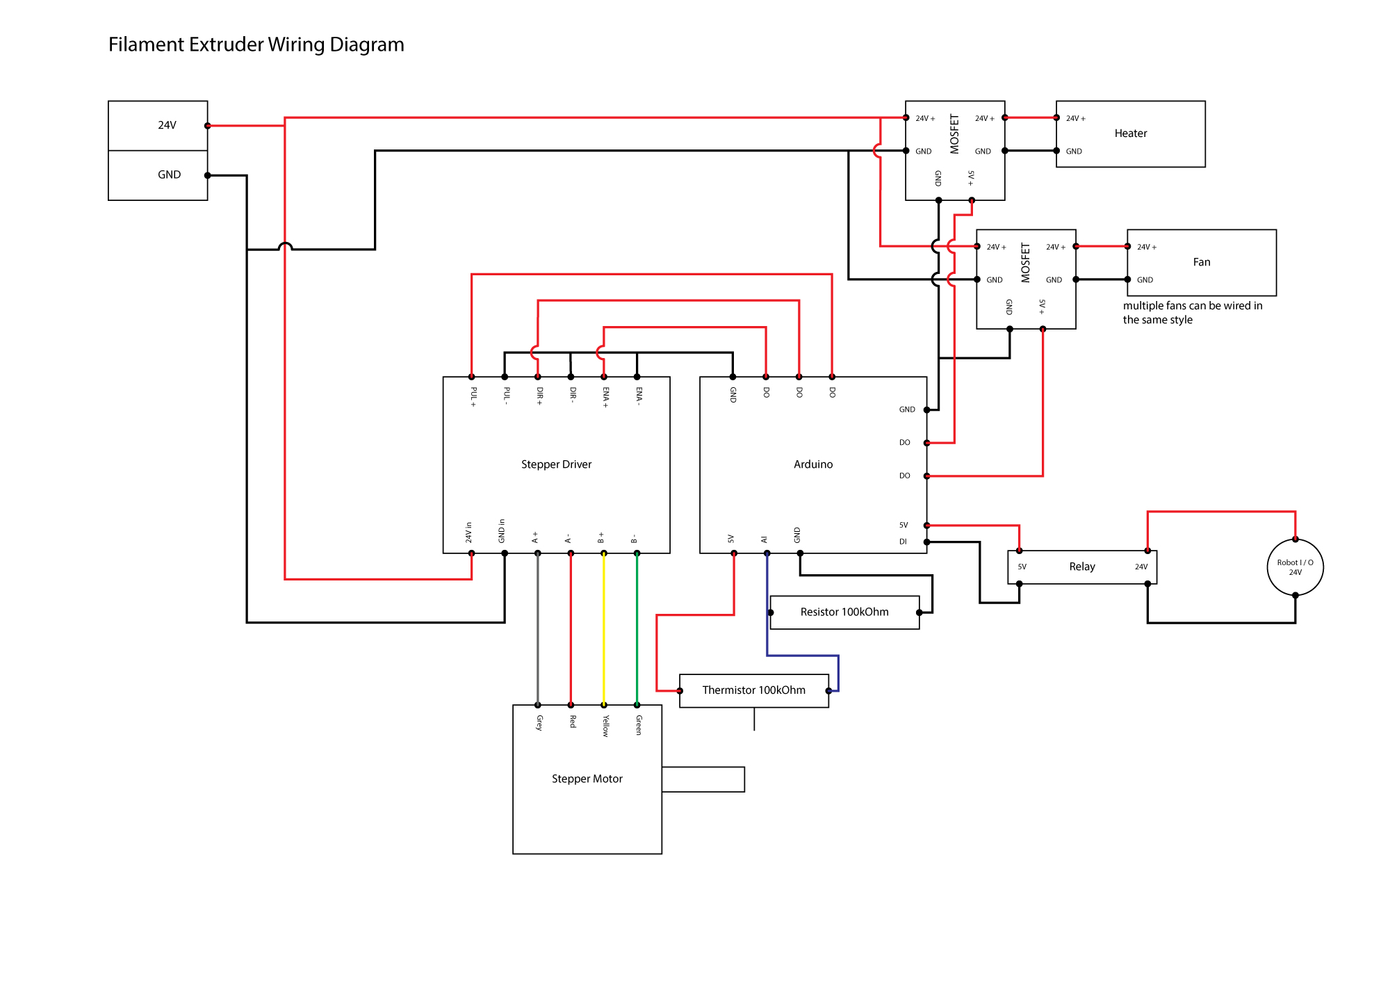
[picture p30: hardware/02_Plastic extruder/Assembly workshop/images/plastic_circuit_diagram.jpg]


1. Connect the four cables from the stepper motor to the stepper motor driver
    - Blue: B-
    - Red: B+
    - Yellow: A-
    - Black: A+

1. Connect the stepper driver outputs to the Arduino.
    - ENA - Arduino GND (on breadboard)
    - ENA + Arduino pin PWM 11
    - DIR - Arduino GND (on breadboard)
    - DIR + Arduino pin PWM 12
    - PUL - Arduino GND (on breadboard)
    - PUL + Arduino pin PWM 13

1. Put the stepper driver setting pins in the right position (800 microsteps / 1.5A): 
    1. ON
    1. OFF
    1. OFF
    1. ON
    1. ON
    1. OFF

1. Connect the MOSFET board which controls heating (note: MOSFET board needs to be soldered first, ask us before placing components)
    - TRIG/PWN > Arduino pin PWN5
    - GND > Arduino GND (on breadboard)
    - Vin + 24v power supply +
    - Vin - 24v power supply -
    - OUT + One end of heating element cable
    - OUT - Other end of heating element cable

1. Connect the MOSFET board which controls the fan (note: MOSFET board needs to be soldered first, ask us before placing components)
    - TRIG/PWN > Arduino pin PWM2
    - GND > Arduino GND (on breadboard)
    - Vin + 24v power supply +
    - Vin - 24v power supply -
    - OUT + One end of fan cable
    - OUT - Other end of fan cable

1. Read this guide on Arduino Thermistors: http://www.circuitbasics.com/arduino-thermistor-temperature-sensor-tutorial/  
    - Connect the output to the Arduino Analog In 0 (A0)

1. Connect the relay cabling according to the picture or example
    - Connect the robot I/O (Digital Output) to the relay.

1. Connect your laptop to the Arduino and upload the code which can be found in: *mini_eggshell\software\02_Arduino\plastic_extruder_arduino* 

1. Check the temperature using the Thermistor, turn the stepper motor on/off using the robot I/O and see if the fans are working. 

1. Profit!

# Clay extruder

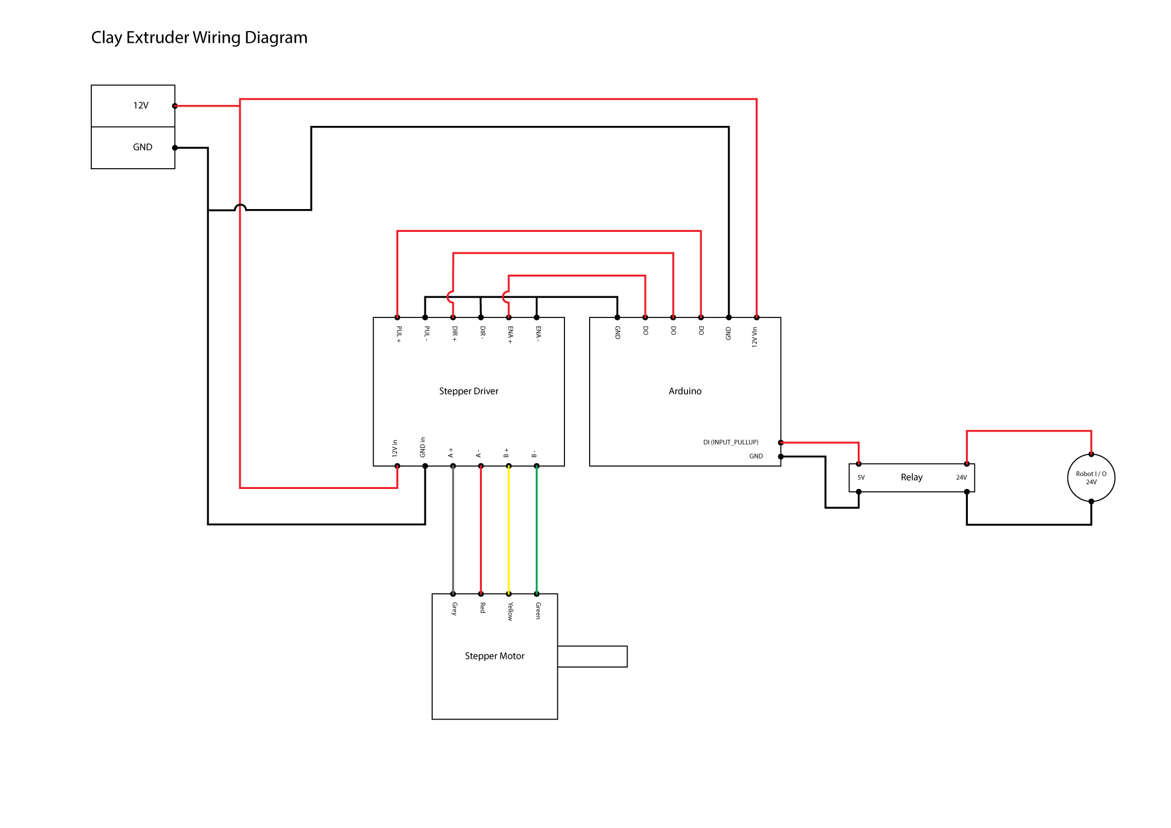
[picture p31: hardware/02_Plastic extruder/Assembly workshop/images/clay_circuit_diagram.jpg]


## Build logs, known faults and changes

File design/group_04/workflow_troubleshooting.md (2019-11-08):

# Workflow and troubleshooting

## Workflow

### Open files

1. Pull `mini_eggshell`.
2. Open VSCode, open folder with git repo `mini_eggshell`
3. Open `Base.3dm` (in `mini_eggshell/design/group_04`)
4. Open `ur_online_control_gh_group_04.gh` in `mini_eggshell/ur_online_control/grasshopper`

### Settings (in grasshopper)

1. Ping robot using the ping node in the grasshopper document.
2. Set base if needed using `get_pose_cartesian` and copy the output to `base` node
3. Measure distance from nozzle to bottom of plastic holder, input the result using the slider connected to the tool cluster.

### Input geometry

1. Create points or frames using slicer in grasshopper document or loading from `ghdata` file using `Data Input` node. (If you get an error on the `Data Input` node right click and double check that it's loading from the right folder, then disable and enable it)
2. Move the `safe_pt` point to a good location, best is above the geometry to be printed.
3. Rotate planes if needed so that the tool is in a good position, including the safe\_pt plane.

### Run script

1. Run the script using the bat-file located on your Desktop. `Win+D` shows the Desktop, which is a quick way to get to the `run_print.bat` file.

### Sharing and updating files

Changes to these files should be pushed at least at the end of day:

- `ur_online_control_gh_group_04.gh`
- `main_direct_send_group_04.py`
- `base.3dm`
- and any other files that's used in the printing

Other files not directly linked to running the robot should be shared using our Dropbox folder.

## Troubleshooting

### No clay coming out

- Make sure the clay is wet.
- Make sure that the top caps plastic seal is clean and that the top cap is screwed on hard.
- Make sure that there's not dry clay in the end of the nozzle.

### Slow grasshopper document

- Don't send too many planes, send a few using split list and then rerun it using the rest.

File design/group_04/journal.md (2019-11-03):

# Journal

[Markdown cheatsheet](https://github.com/adam-p/markdown-here/wiki/Markdown-Cheatsheet)

## 2019-10-29

Working on design propsal and goals.

* Create column by simultaneous clay printing and concrete casting, with the structural goal of creating supports on the column for (horisontal) beams.
* Explore joint geometry, e.g. articulated joints (inspired by skeletal joints) or restrained joints.
* Exploration of clay overhangs while simultaneously casting.

End goal: 2 colums 1 beam

### Challenges
* clay formwork: max overhang for the support of the beam. Add micro-structure to the faces of the beam 
* structural purpose: opitmize interface column and beam 

### References
* <https://www.instagram.com/p/BizeScmlkPr/?utm_source=ig_web_copy_link>
* <https://www.instagram.com/p/BuGGrv2iORI/>

## 2019-10-30

### Desk crit with Joris and Nizar

Explained concept, joints of different kinds. Noise.

We talked about using axolotl and Emmanuelle's gh script to get the nice boolean operations of volumetric modeling.

Nizar was clear that the joint should be the focus, and noise/texture an addition.

Nizar sketched a column meeting a beam at top of column as a possible design. (Think of a T)

We talked about challenges in clay/concrete printing/casting, overhangs and underhangs, the interaction between concrete and clay.

### Discussion after

Explore joint typolgies, maybe focus on each.

We should branch (maybe) out to look at non console joints, with an imaginary (or real) second vertical element.

The three could be:
* the T-like assemblage
* a angled beam sticking into the column 
* a horisontal beam meeting the vertical column.

### References
* [Polymorf, people Anton worked together with on clayprinting](http://polymorf.se/)
* [Swallow's nest](https://tetov.se/swallows-nests/) and [LISp](https://tetov.se/lisp-non-planar-tile-fabrication/) two clay projects by Anton.
* [Weird wooden laser cut joints](https://gkirdeikis.wordpress.com/portfolio/aggregation-and-graph-based-modeling/) by Gediminias Kirdeikis

## 2019-10-31

Extruder assembly all day, setting up arduino to control stepper motor, heating block & fan (for the plastic extruders), and air pressure for the clay extruders.

## 2019-11-01

### Presentation

Main take-away was to go for some sort of bridging beam between two columns?

### First test prints

During afternoon-evening we printed three test prints, all starting with a circle at z0 and then a spiral. Layer height for the first two were 1 mm and the third was 2 mm.

Issues with "filament loading point" and when to turn on air pressure and extruder that needs to be resolved. Also weird last move during print; goes straight down destroying print.

Aluminium can too close to last joint of robot, need new holder.

## 2019-11-03

New holder for extruder ready to be printed tomorrow.

Added new tool assembly to gh script in ur_online_control, as well as the polymorph slicer cluster.

Created a test geometry we can print to explore overhangs and simultaneous casting.

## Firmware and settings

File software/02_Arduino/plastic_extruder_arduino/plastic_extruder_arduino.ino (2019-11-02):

// ===============================================================================
// CONSTANTS 
// ===============================================================================

// Stepper library created by Mike McCauley, install from Tools > Manage Libraries
#include <AccelStepper.h>

// Stepper motor pins
#define enablePin 11 // ENA - Enable
#define dirPin 12 // DIR - Direction
#define stepPin 13 // STP/PUL - Step, Pulse
#define motorInterfaceType 1

#define thermistorPin A0 // AnalogIn Pin A0

#define urPin 8

#define fanPin 2

#define heatingPin 5

unsigned long previousMillis = 0; // will store last time PRINT was updated
const long tempCheckInterval = 1000; // interval at which to check temperature

// THERMISTOR CONSTANTS
int Vo;
float R1 = 1000;
float logR2, R2, T, Tc, Tf;

// Obtained c values from: 
// https://www.thinksrs.com/downloads/programs/Therm%20Calc/NTCCalibrator/NTCcalculator.htm
//float c1 = 1.009249522e-03, c2 = 2.378405444e-04, c3 = 2.019202697e-07;
float c1 = 0.8098138332e-3, c2 = 2.115966516e-4, c3 = 0.7086146145e-7;
//float c1 =0.7203283552e-3, c2 = 2.171656865e-4, c3 = 0.8706070062e-7;

// ===============================================================================
// VARIABLES
// ===============================================================================

#define SET_TEMP 200
#define MOTOR_SPEED 900

// ===============================================================================
// STEPPER MOTOR
// ===============================================================================

// Stepper motor = NEMA 17 Schrittmotor 1.8 Grad, 1.5A (3Dware.ch)
// https://www.3dware.ch/NEMA-17-Schrittmotor-1.8-Grad,-1.5A-De.htm 
// setSpeed(): Set the speed in steps per second:
// Driver is set to 3200 steps / revolution
// This means setSpeed(3200) will give 1 revolution / second

// Create a new instance of the AccelStepper class:
AccelStepper stepper = AccelStepper(1, stepPin, dirPin);

void rotateStepper(){
  // Rotates the stepper motor with a desired speed
  stepper.runSpeed();
}

// ===============================================================================
// THERMISTOR
// ===============================================================================

void temperatureControl(){
  unsigned long currentMillis = millis();
  if (currentMillis - previousMillis >= tempCheckInterval) {
    // save the last time temperature was checked
    previousMillis = currentMillis;
    
  // Read the temperature from the thermistor
  Vo = analogRead(thermistorPin);

  // Convert voltage to temperature
  R2 = R1 * (1023.0 / (float)Vo - 1.0);
  logR2 = log(R2);
  T = (1.0 / (c1 + c2*logR2 + c3*logR2*logR2*logR2));
  Tc = T - 273.15;

  // Print output
  Serial.print(" Temperature: "); 
  Serial.print(Tc);
  Serial.print(" C // ");   
  Serial.print(" Set Temp: ");
  Serial.print(SET_TEMP);
  Serial.println(" C"); 

  if (Tc < SET_TEMP){
    analogWrite(heatingPin, 255);
    Serial.print(" Heater ON // ");
    }
  else {
    digitalWrite(heatingPin, LOW);
    Serial.print(" Heater OFF //");
   }  
  }
}

// ===============================================================================
// SETUP
// ===============================================================================

void setup() {
  // Set the maximum speed in steps per second:
  stepper.setMaxSpeed(3200);
  stepper.setSpeed(MOTOR_SPEED);

  // Setup Thermistor
  Serial.begin(9600);

  // Enable UR pin
  pinMode(urPin, INPUT_PULLUP);
}

// ===============================================================================
// LOOP
// ===============================================================================

void loop() {
  analogWrite(fanPin, 255); // Turn the fan on
  temperatureControl(); // Check temperature and turn on heater
  if (digitalRead(urPin) == LOW) { // If I/O DO 4 is enabled:
    rotateStepper(); // Rotate the stepper motor
    
    }
  else {
    analogWrite(fanPin, 0); // Turn the fan off
  }
  }

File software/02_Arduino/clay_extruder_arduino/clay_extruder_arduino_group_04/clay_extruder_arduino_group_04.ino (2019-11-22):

// WIP!!!

// Stepper library created by Mike McCauley, install from Tools > Manage Libraries
#include <AccelStepper.h>

//defines pins
const int stepPin = 6; // PUL - Pulse
const int dirPin = 7;  // DIR - Direction
const int enPin = 8;   // ENA - Enable
const int urPin = 4;   // UR io via relay
const int MOTOR_SPEED = 1100;
const int RETRACTION_DISTANCE = 22000;
int pinState;
bool running = 0;

// ===============================================================================
// STEPPER MOTOR
// ===============================================================================
// setSpeed(): Set the speed in steps per second:
// Driver is set to 200 steps / revolution
// This means setSpeed(3200) will give 16 revolution / second
// Create a new instance of the AccelStepper class:

AccelStepper stepper = AccelStepper(1, stepPin, dirPin);

void extrude()
{
  // Rotates the stepper motor with a desired speed
  // Speed is negative to make it go CW

  // Serial.println("Extruding");
  stepper.runSpeed();

}

void retract()
{
  // Serial.println("Retracting");
  bool notFinished = 1;

  // Positive goal and speed to run CCW
  stepper.setCurrentPosition(0); // unneccessary?
  stepper.moveTo(RETRACTION_DISTANCE);
  stepper.setSpeed(MOTOR_SPEED);

  while (notFinished == 1)
  {
    // returns true when reached position
    notFinished = stepper.runSpeedToPosition();
  }

  // reset the speed for extrusion
  stepper.setSpeed(-MOTOR_SPEED);
}

void setup()
{
  // Set the maximum speed in steps per second:
  stepper.setMaxSpeed(3200);
  stepper.setSpeed(-MOTOR_SPEED);

  // Serial.begin(9600);
  // Serial.println("Hello World!");

  pinMode(urPin, INPUT_PULLUP);
}

void loop()
{
  pinState = digitalRead(urPin);

  if (pinState == HIGH && running == 0)
  {
    retract();
    running = 1;
  }
  else if (pinState == LOW)
  {
    extrude();
    running = 0;
  }
}

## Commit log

2019-10-25 Added folder structure, literature
    [101024_Concrete_mixdesign_mini_Eggshell_.xlsx]
2019-10-26 UR Plastic and Clay end effectors
    [clay_extruder_endEffector_V5.3dm]
2019-10-26 Bachmann UR base partial model
    [bachmann_ur_base.3dm]
2019-10-26 UR online control files added
    [measurement_tool.obj, measurement_tool.stp]
2019-10-28 Updated concrete recipe and added intro presentation
    [101024_Concrete_mixdesign_mini_Eggshell_.xlsx]
2019-10-28 Arduino code for clay extruders
2019-10-29 First day
    [Base.3dm]
2019-10-29 Calibrate Z position to match Robot with Rhino Visualization
2019-10-29 Added plastic extruder Arduino files, changed naming of clay extruder Arduino
2019-10-31 Uploaded files for extruder assembly workshop
2019-10-31 Updated assembly workshop files and added circuit diagrams for plastic/clay
2019-10-31 correct extruder tool models
    [191030_plastic_extruder.stl]
2019-11-02 1st day working with clay extruder, testing the motor and air pressure in relation with digital output
2019-11-02 Changes to setup after first day of printing
    [Base.3dm]
2019-11-02 Updated Arduino file to include new resistor (1kOhm instead of 120kOhm)
2019-11-03 Clay extruder Settings set
    [191101_BaseTableConfiguration.3dm]
2019-11-03 New holder for clay extruder with alu canister
    [clay_extruder_endEffector_V5.3dm]
2019-11-03 Trying to debug last movement during print
2019-11-04 Overhang test geometry, better start of print
2019-11-05 added filament wooden stand and printing table
    [Pole Filament Prototype.3dm]
2019-11-06 Infilled prototype
    [Base.3dm]
2019-11-07 fixing Jomana Model Path for printing
2019-11-08 Table moved, tcp fixes
    [Base.3dm]
2019-11-08 setup UR10 and do a 2nd print and casting
2019-11-08 Updated files, workflow_troubleshooing added, WIP of new arduino code
    [Base.3dm]
2019-11-08 Updated base and gh script
    [Base.3dm]
2019-11-08 End of Day Push
    [Base.3dm]
2019-11-09 Print Jomana Path with 2mm layer thk
2019-11-09 Post DAY 2 Print, Tidy up grasshopper files
2019-11-11 For Non
    [191111_BaseTableConfiguration_geometriesBC.3dm]
2019-11-11 Ready to print
    [191111_BaseTableConfiguration_geometriesBC.3dm]
2019-11-11 Updated 3DM file
    [191111_BaseTableConfiguration_geometriesBC.3dm]
2019-11-11 End of the Day Push, Printing Vase using Sines in Z axis
2019-11-12 New base geometry
    [191111_BaseTableConfiguration_geometriesBC.3dm]
2019-11-12 Adding start stop extruder to movel generator
2019-11-12 Changes to grp 4 arduino code, organized other grps arduino code
2019-11-12 Robot not printing, needs to be troubleshot
2019-11-13 From Fred
    [191111_BaseTableConfiguration_geometriesBC.3dm]
2019-11-13 end of print day 4
2019-11-13 Fixed errors in test print 19
2019-11-14 Sleep after air pressure (because of tube)
2019-11-14 New version three branches, also updates arduino
2019-11-14 set up new printing base, for final model print
2019-11-15 Start printing push
2019-11-15 big print trial
2019-11-16 Fixed state machine I think
    [clay_extruder_arduino_group_04.ino]
2019-11-19 Fixes to cylinder print
2019-11-19 Fixed print
2019-11-19 Anton fix division legs
2019-11-20 Cylinder print
2019-11-20 Final Print Grasshopper File
2019-11-20 Fixes to cylinder
2019-11-20 Updated the base
    [Base.3dm]
2019-11-22 slicer update
    [101024_Concrete_mixdesign_mini_Eggshell_COLOMATC_MIXER.xlsx]
